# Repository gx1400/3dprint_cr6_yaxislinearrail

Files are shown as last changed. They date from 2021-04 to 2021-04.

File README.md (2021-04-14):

# CR-6 SE Y-axis Linear rail and MGN12H carriage mount

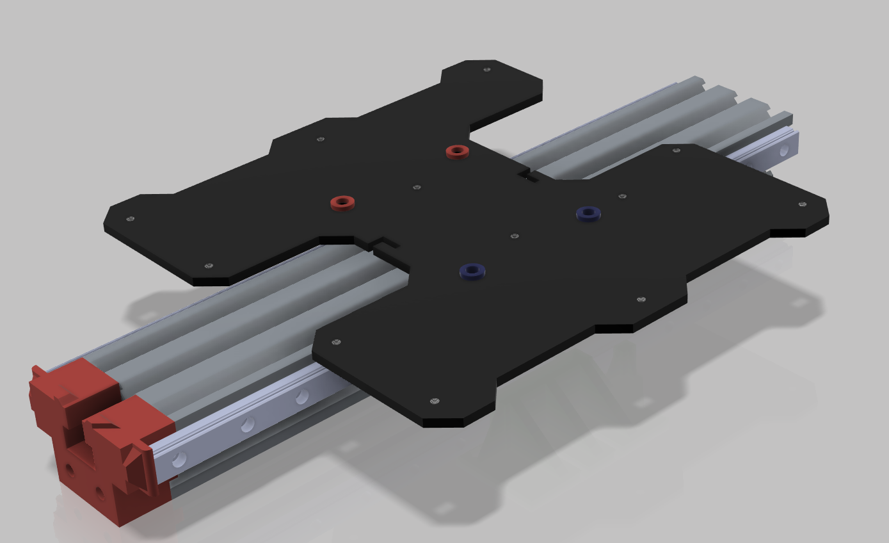
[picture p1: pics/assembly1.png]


THIS PROJECT IS UNDER DEVELOPMENT

This conversion method DOES require you to replace the Y-axis belt, but unlike some other projects doesn't require you to cut the rail.

Required Supplies:
- 2x 350mm long MGN rail with MGN12H carriage.  [I bought this](https://smile.amazon.com/gp/product/B07SPQZ383/) because it was cheap and fast, I would recommend Hiwin.
- [GT2 timing belt](https://smile.amazon.com/gp/product/B07ZNNR238/) (this solution requires longer belt. will have to crimp yourself as well).
- 2x M5x30 mm button head or socket head screws (attach spacer to tensioner)
- 4x M5x10 mm button head or socket head screws (attach build plate carriage to brackets)
- 4x M5 nut or nylock nut (I used nylock nut, press into left and right brackets with pliers)
- 20x M3x8mm button head or socket head screws (attach rails to extrusion & bracket to tensioner)
- (optional) M3 nuts (for slide-in t-nuts if you choose to print your own, see notes.  Press in with pliers)
- (optional) [Alignment blocks for linear rail to 2020 extrusion](https://www.thingiverse.com/thing:2804412)

[Thingiverse Thing link](https://www.thingiverse.com/thing:4828178)

# Printed parts

## 'plate bracket left.stl'

This part mounts to the left side carriage and interfaces with the build plate carriage.  Need to press in M5 nuts or nylock nuts.

Suggested printing:
- 0.2mm layer
- 50% infill, Gyroid
- 4 walls
- Top touching build plate.  No supports.

## 'plate bracket right.stl'

This part mounts to the right side carriage and interfaces with the build plate carriage.  Need to press in M5 nuts or nylock nuts.  This part interfaces with the y-axis end stop/homing switch.

Suggested printing:
- 0.2mm layer
- 50% infill, Gyroid
- 4 walls
- Top touching build plate.  No supports.

## 'spacer_5mm.stl'

This part provides proper spacing to make sure the left side M5x10 screws do not bottom out on the linear rail when tightened to connect carriage to bracket

Suggested printing:
- 0.12mm layer
- 100% infill
- 4 walls (should be pretty much all walls...)
- No supports

## 'spacer_7mm.stl'

This part provides proper spacing to make sure the right side M5x10 screws do not bottom out on the linear rail when tightened to connect carriage to bracket.  In addition, since these holes are larger to accomodate the eccentric hex spacer on stock install.  This centers the screw to help remove slop.

Suggested printing:
- 0.12mm layer
- 100% infill
- 4 walls (should be pretty much all walls...)
- Top touching build plate.  No supports.

## Tensioner adapter

Since the linear rails are readily available in lengths of 300 and 350 mm, but 300mm is too short and 350 is too long; this adapter allows you to mount 350 mm rail without cutting the rail.  This part will also double as an end-stop for the front piecepart.

Suggested printing:
- 0.2mm layer
- 10-20% infill, Gyroid
- 3 walls
- Front side touching build plate.  Enable Supports (should just be the end stop sides that jut out, may not even be needed)

## OPTIONAL: 'rail nut m3-2x.stl'

See notes.  I used these to slide into extrusion.  I had to make them very thin to fit into the OpenBuilds extrusion I was experimenting with at my desk, turns out when I went to Creality extrusion, there are significantly different extrusion dimensions.  I ended up getting some plastic deformation when torquing down.  I'm buying metal T-nuts.

I prefer the double nut version over the single nut version below.  Your choice.

M3 nuts can be pressed in with pliers

Suggested printing:
- 0.12mm layer
- 100% infill
- 3 walls (should be pretty much all walls...)
- Top touching build plate.  No supports.

## OPTIONAL: 'rail nut m3-1x.stl'

See notes and text above in 'rail nut m3-2x.stl.

## OPTIONAL: 'vrail spacer m3.stl'

I used this to help keep the MGN rail out of the extrusion slot.  Probably not needed.

Suggested printing:
- 0.12mm layer
- 100% infill
- 3 walls 
- Top touching build plate.  No supports.

# Notes

- I used the printed t-nuts ('rail nut m3-2x.stl'), but found the plastic was pretty thin and gave under torque.  I'm ordering some metal slide in t-nuts from amazon ([This one](https://smile.amazon.com/gp/product/B075SY9Y96/) and [This one](https://smile.amazon.com/gp/product/B0841G5SB1/) to see how they fit.  I expect they will be more durable and secure.

# License

[Creative Commons - Attribution - Non-Commercial (CC BY-NC 3.0)](https://creativecommons.org/licenses/by-nc/3.0/)

# Changelog

2021/04/15 - Update readme instructions

2021/04/14 - Updated design files

2021/04/11 - Initial commit

## Design

Autocad Fusion 360 

## Slicer

Ultimaker Cura 4.8.0
- Printer: Creality CR6 SE
- Layer Height: 0.x mm
- Infill Density: xx%
- Infill Pattern: Gyroid
- Filament: Inland PLA+ 1.75mm Neon Green
- Material: PLA+
- Print Temperature: 215 degrees C

# Pics

# Model Views

Ortho View Ortho view
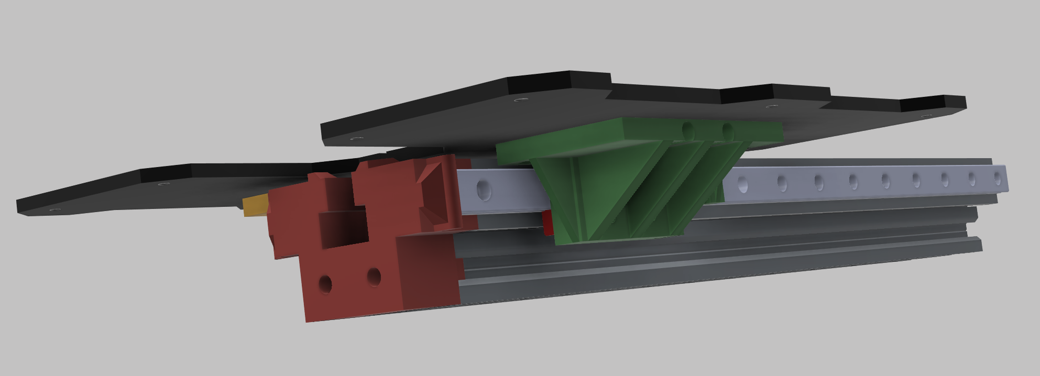
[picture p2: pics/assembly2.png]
Under View Under view

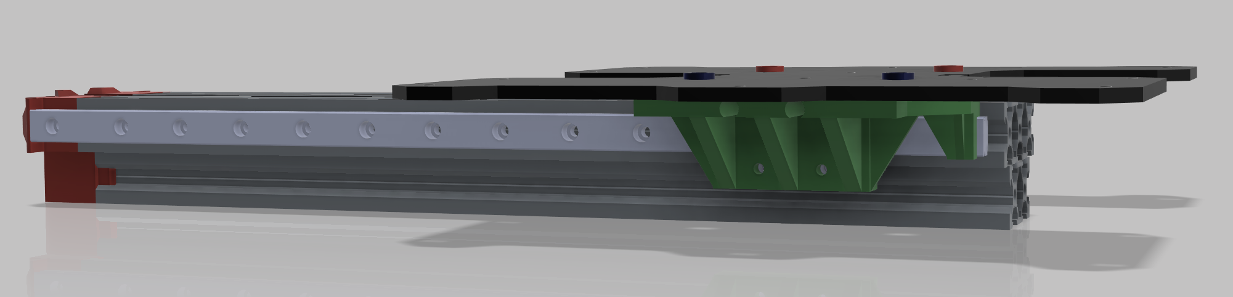
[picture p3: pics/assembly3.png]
Back right view

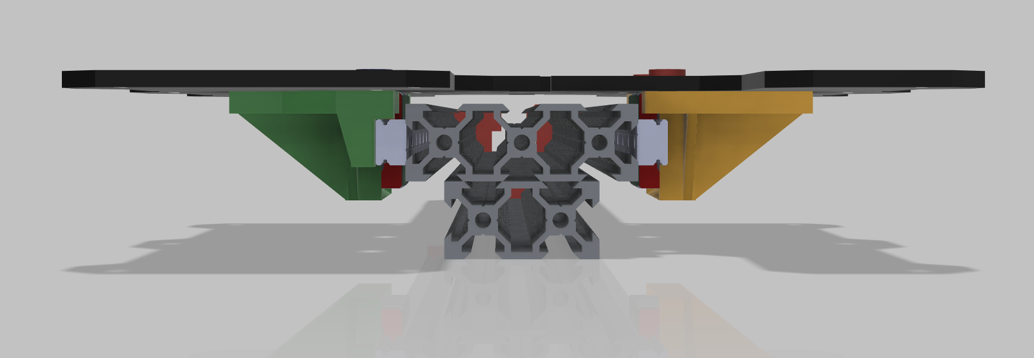
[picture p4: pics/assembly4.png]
Rear view


# T-nuts (optional)
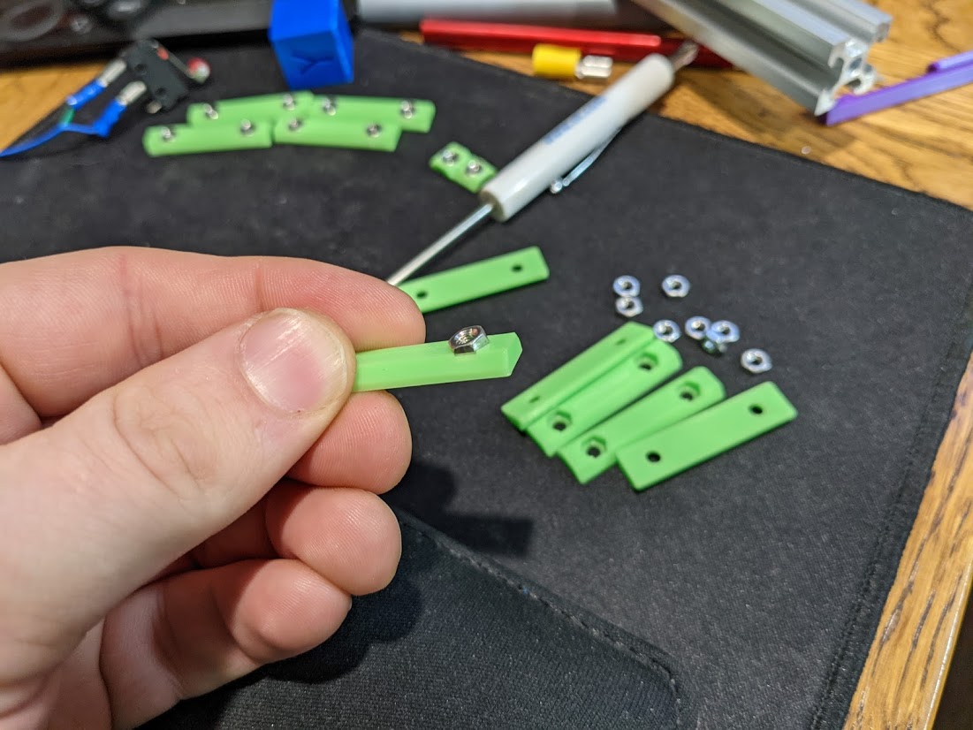
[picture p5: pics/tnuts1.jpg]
T-nut ready for pressing T nut ready for pressing

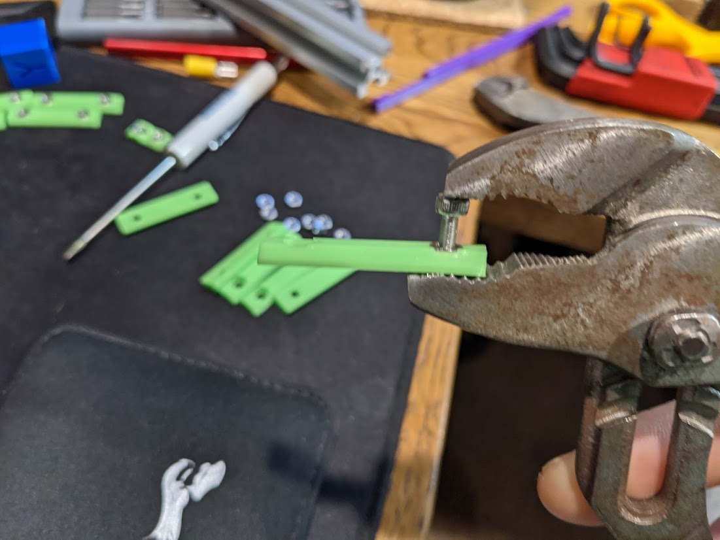
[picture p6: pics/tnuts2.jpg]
T-nut press in more

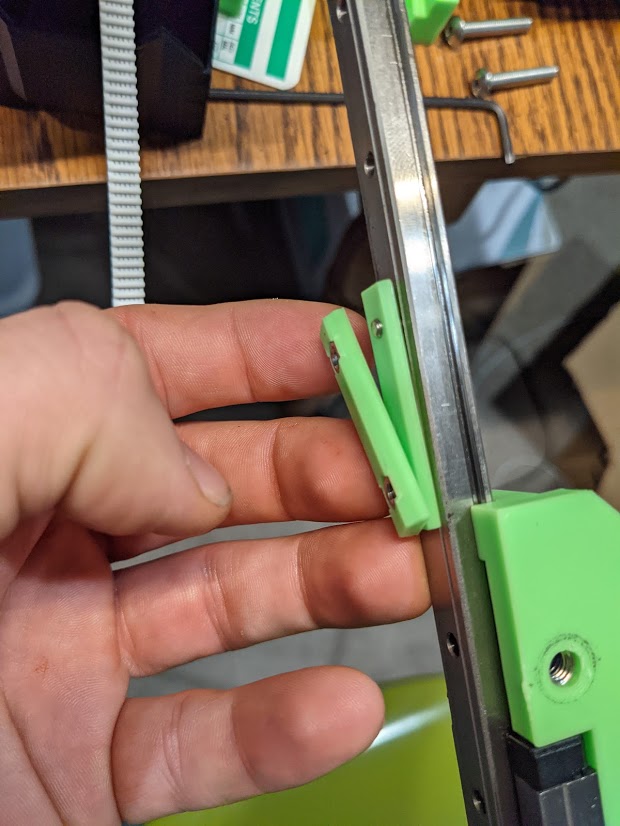
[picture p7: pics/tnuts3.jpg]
T-nut and spacer
 "T-nut and spacer")

# Adapter
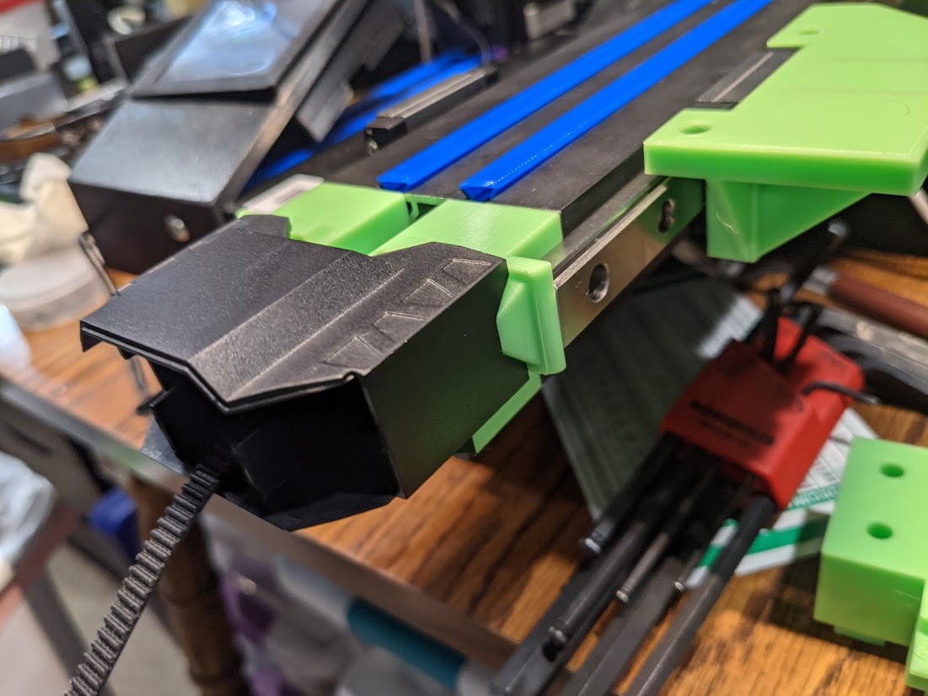
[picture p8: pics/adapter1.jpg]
Adapter front ortho view

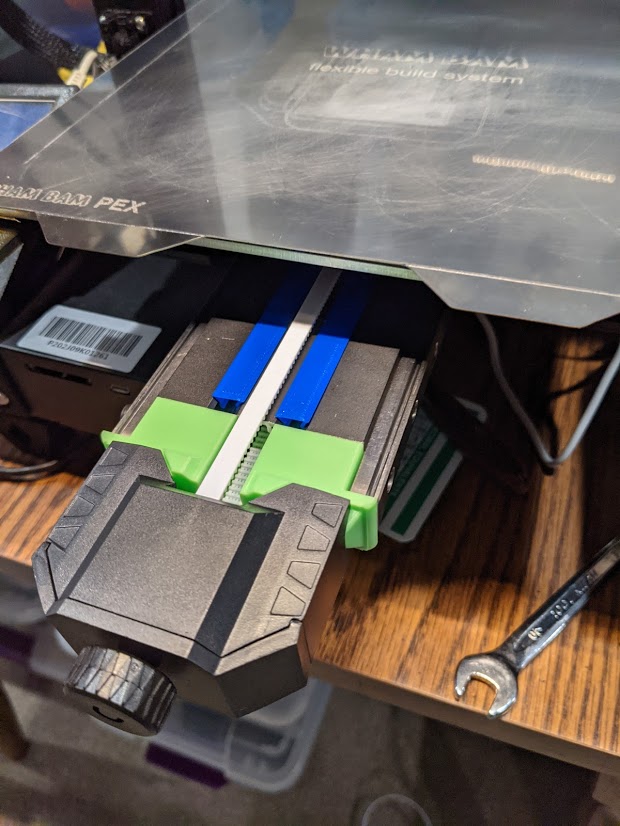
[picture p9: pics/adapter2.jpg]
Adapter topish view


# Linear rail
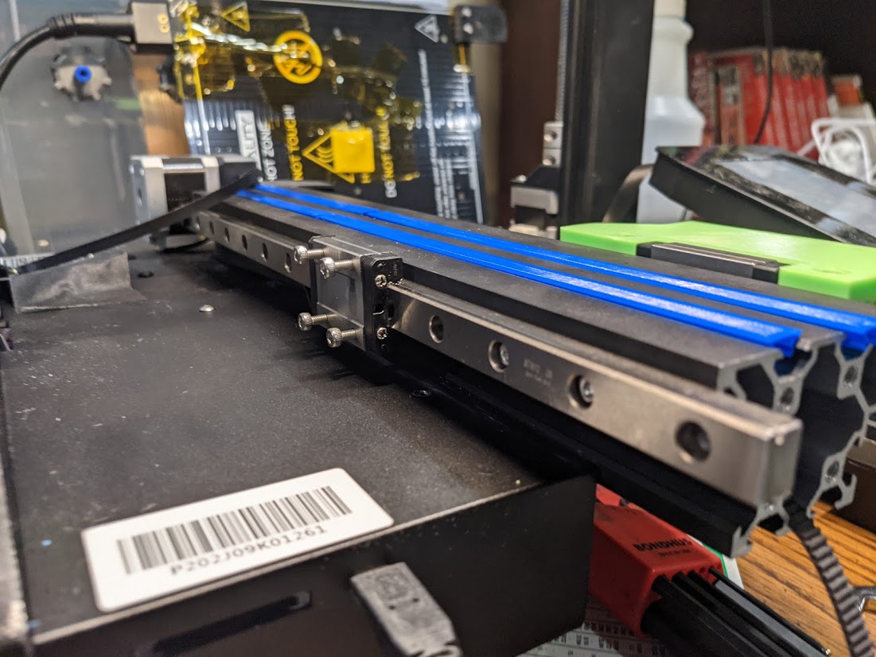
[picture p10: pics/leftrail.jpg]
Left rail install

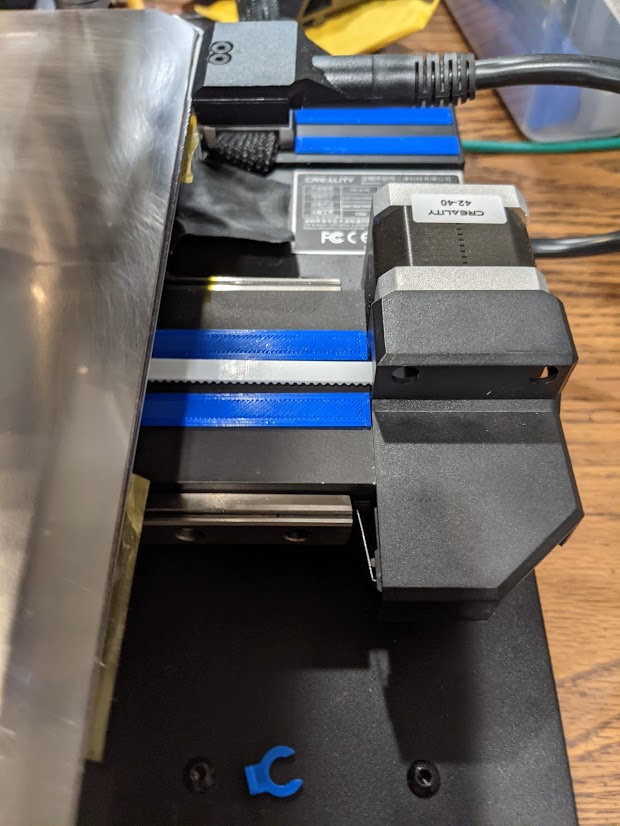
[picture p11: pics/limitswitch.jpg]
Right rail limit switch placement right rail limit switch placement

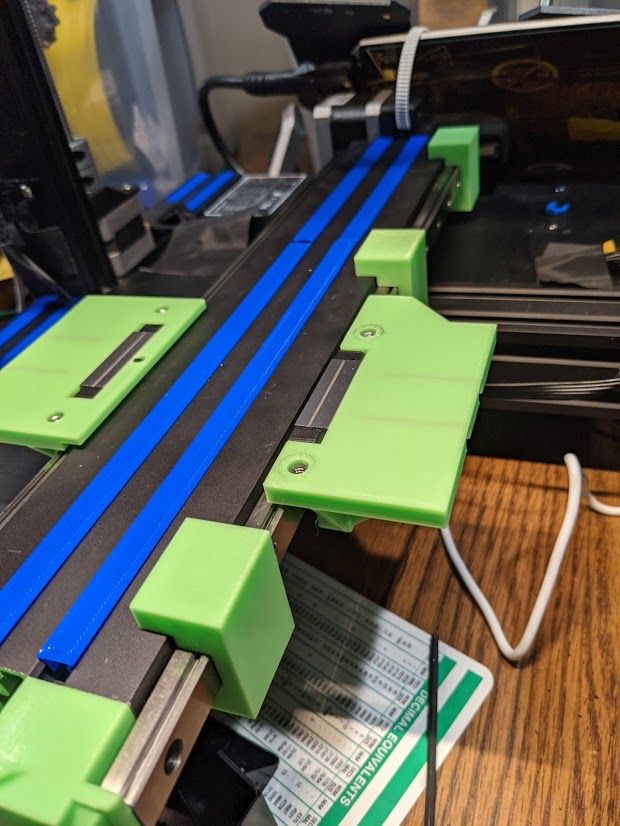
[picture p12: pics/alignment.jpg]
Rail alignment


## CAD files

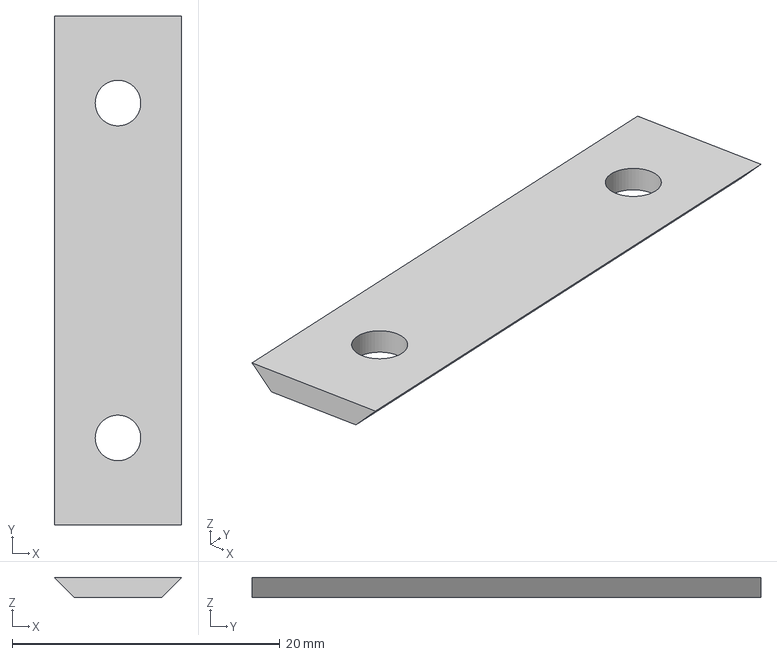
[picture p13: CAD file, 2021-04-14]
vrail spacer m3.step
9.50 x 38.0 x 1.50 mm

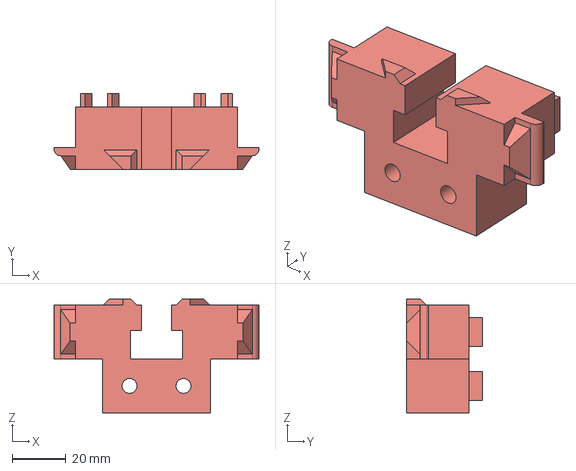
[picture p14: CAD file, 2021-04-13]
tensioner adapter.step
76.0 x 28.0 x 42.2 mm

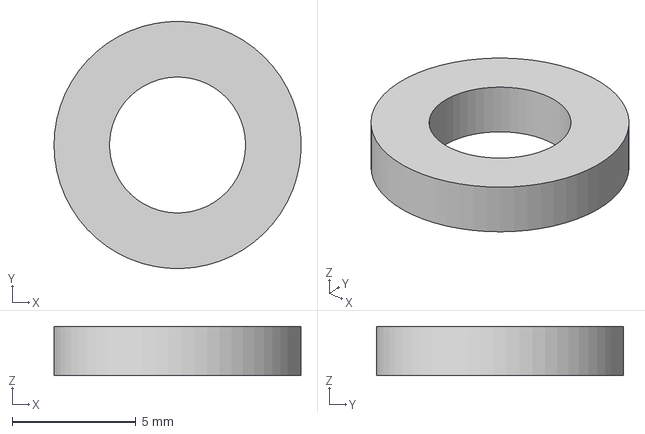
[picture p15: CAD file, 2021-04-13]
spacer_5mm.step
9.99 x 10.00 x 2.00 mm

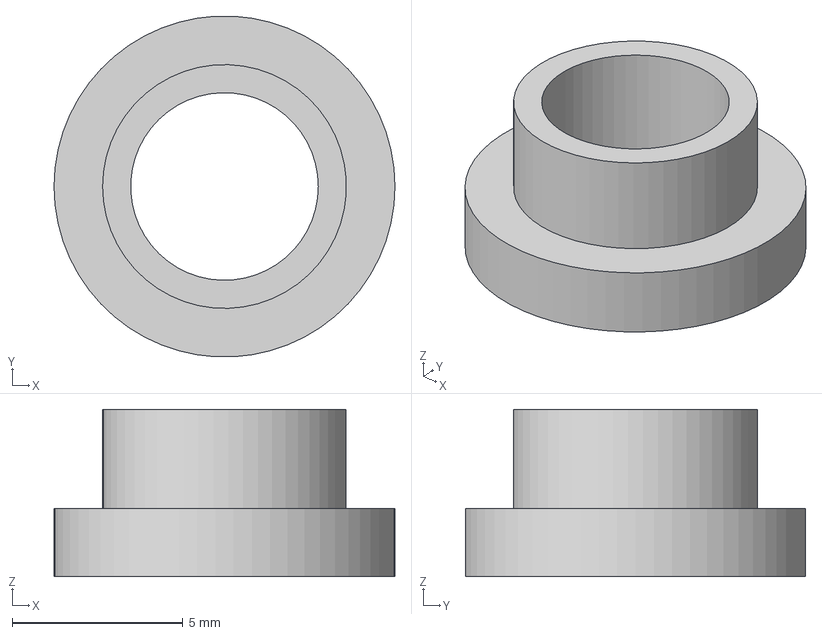
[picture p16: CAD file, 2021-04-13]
spacer_7mm.step
10.0 x 9.99 x 4.90 mm

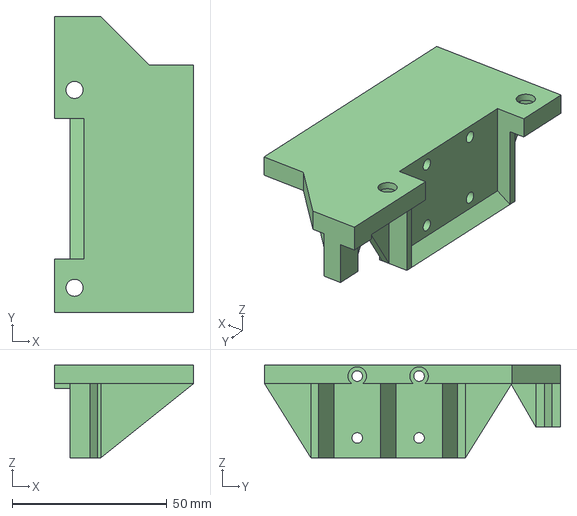
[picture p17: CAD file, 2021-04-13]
plate_bracket-right.step
45.0 x 95.8 x 30.0 mm

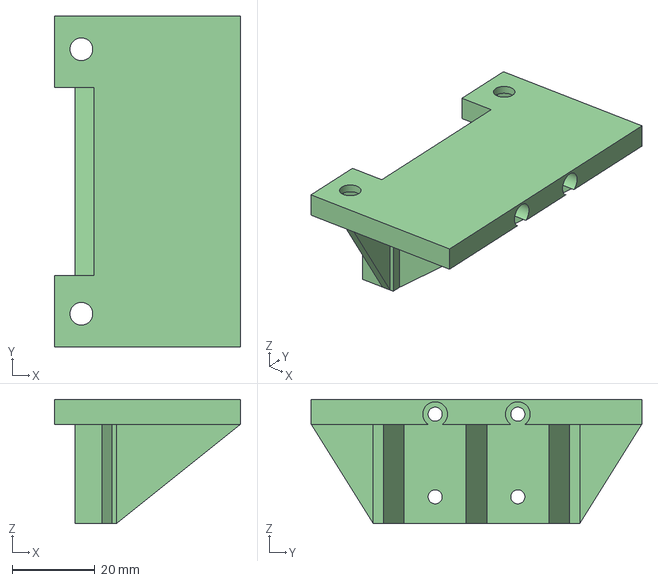
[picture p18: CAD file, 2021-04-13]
plate_bracket-left.step
45.0 x 80.0 x 30.0 mm

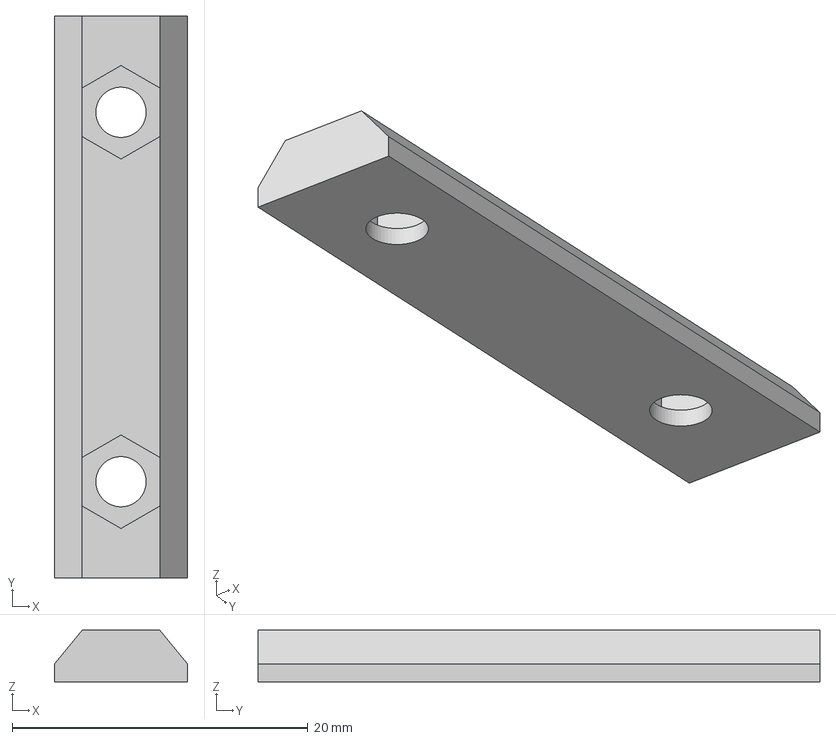
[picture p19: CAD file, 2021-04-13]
rail nut m3-2x.step
9.00 x 38.0 x 3.50 mm

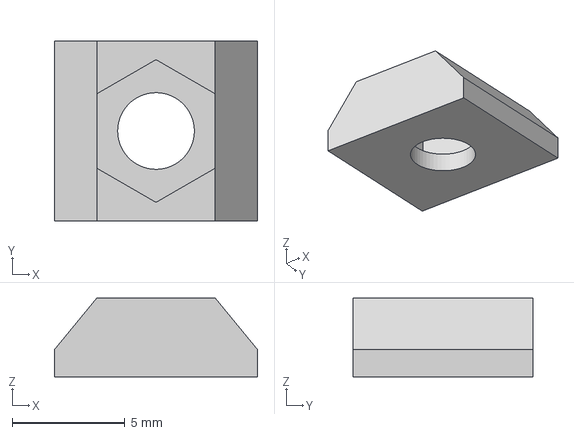
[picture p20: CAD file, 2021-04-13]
rail nut m3-1x.step
9.00 x 8.00 x 3.50 mm

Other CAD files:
spacer.step
CR6_yaxis.f3z
plate_bracket-left.f3d
plate_bracket-left.stl
plate_bracket-right.f3d
plate_bracket-right.stl
rail nut m3-1x.f3d
rail nut m3-1x.stl
rail nut m3-2x.f3d
rail nut m3-2x.stl
spacer_5mm.f3d
spacer_5mm.stl
spacer_7mm.f3d
spacer_7mm.stl
tensioner adapter.f3d
tensioner adapter.stl
vrail spacer m3.f3d
vrail spacer m3.stl

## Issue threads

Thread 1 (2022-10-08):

Looking for an update.

fairwood136, 2022-10-08:
I'm looking at implementing your solution for the y-axis.  I'm wondering if you can provide an update on how it is working for you.  It looks like you also modified the tensioner for the y-axis as well.

Any regrets with the quick and cheap linear rails.  If I can source 330mm rails is that better than using the 350mm ones?  Or is there a different measurement to use?

Thanks.

gx1400, 2022-10-08:
No real feedback, it works well enough for me. But I make no promises!

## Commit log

2021-04-12 work in progress, updated brackets, untested spacer, exports.
    [belt tensioner spacer.f3d, belt tensioner spacer.step, belt tensioner spacer.stl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]
2021-04-12 add readme and f3z
    [CR6_yaxis_assy.f3z]
2021-04-12 fix pictures
    [plate_bracket v3.stl]
2021-04-13 reexport updated files
    [CR6_yaxis_assy.f3z, belt tensioner spacer.f3d, belt tensioner spacer.step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]
2021-04-13 new assy export
    [CR6_yaxis.f3z]
2021-04-14 more pics
    [vrail spacer m3.f3d, vrail spacer m3.step, vrail spacer m3.stl]
